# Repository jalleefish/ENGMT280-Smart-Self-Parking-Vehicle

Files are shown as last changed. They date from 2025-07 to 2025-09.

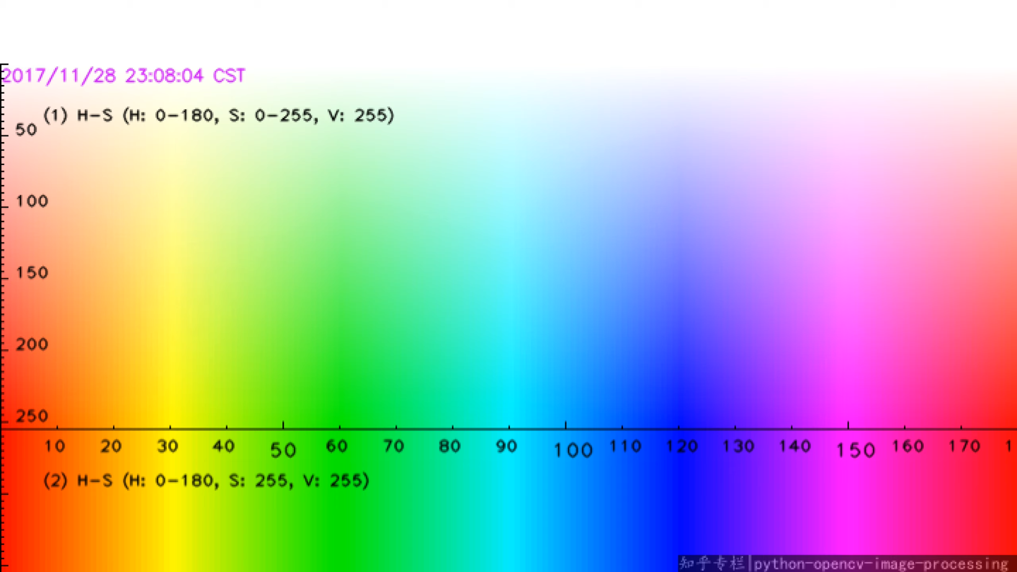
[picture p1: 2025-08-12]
System Logic/Drafts/Image Processing Code/HSV Colour Chart.png

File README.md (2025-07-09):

# ENGMT280-Smart-Self-Parking-Vehicle
ENGMT280/ENGEE281 – 25B
Smart Self-parking Vehicle – Design Rules
A scaled version of a typical car park layout will be setup in D.2.03 and C.1.12 (eventually). So
please make sure to feel free to switch lab spaces during the later half of the trimester to have a
go at testing your systems on the track. Below are the design requirements and design constraints
that needs to met by the Smart self-parking vehicle (SSV) you design, while meeting the event
regulations.




Fig. 1(top). Arena for the SSV showing the starting point and the parking bays and (bottom)
Colored tiles placed at the parking bay’s rear wall and parking sensors to check successful vehicle
parking.
ENGMT280/ENGEE281 – 25B
1. Your SAV, once ‘started’, should be able to complete the task autonomously – i.e., no user
inputs from any sort of wired or wireless communication sources once the SSV starts to move.
2. The only form of external communication once your SSV starts is the camera feed going
between the SSV and your laptop/pc for image processing and the processed image’s info
being sent back to the SSV.
3. The SSV, before it’s switched ‘on’, should be completely within the starting area of the arena
(highlighted by the engraved box along the bottom part of the arena in Fig 1(top))
4. There is no restriction for which side can be chosen to start the SSV from as the arena is
symmetric along the vertical axis as seen from Fig 1 (top)’s orientation. The SSV design team
can choose their preferred starting side. If starting from the left-hand side, the SSV needs to
reverse while steering left into parking position and if starting from the right-hand side, the
SSV needs to reverse while steering right back into the parking bay.
5. There will be a reference tile after the starting point where the reference-coloured tile will
be placed that indicates the color of the parking bay that the SSV can park at.
6. The SSV needs to be able to travel along the parking area’s length while checking for available
spots and simultaneously check if that available spot is indeed a valid parking spot.
7. The reference color tile that the SSV needs to scan will be bicolored or single colored
depending on the event.
8. A bi-colored tile indicates that the 2 different spots the SSV should park at in sequence. For
instance if the reference tile is half red and half yellow, the SSV should park in both spots one
after the other in any order.
9. As a minimum requirement, the SSV should atleast be able to park at a single spot (teams can
request a single-colored tile if that’s all they manage to scan and park at). However, marks
will be awarded accordingly.
10. The scoring sheet will be made available on Moodle near the second half of the trimester.
11. The SSV can in no way cause any damage to any part of the arena including the dummy car
models placed in the parked spots.
12. The overall dimensional and dynamic constraints for the SSV are given below
a. Max Length of SSV – 180 mm
b. Max width of SSV – 80 mm
c. Max height of SSV – 75 mm
d. Absolute wheelbase of the SSV – 120 mm
e. The minimum turning radius for the SSV is – 245.346096 mm (represents the half of
the diametrical distance between the outer wheels of the rear axle of the SSV, while
making an exact 180° turn).
f. The SSV shall not have a differential
drive arrangement (not to be confused
with the use of differential gearbox)
where one wheel is driven intentionally
at a rate different from the other wheel
on the same axle that causes the chassis
to pivot with a sharper turning radius
(see Fig 2 for an example of differential
drive robot) Fig.2. Example of a differential drive
robot (which is not allowed)



ENGMT280/ENGEE281 – 25B
g. If the use of some standard parts causes the width of the SSV to be slightly higher than
the allowed SSV width, the teaching team may allow it.
14. All the colored tiles and the reference tile will only be placed after the SSV starts moving.
15. The order of colours tiles placed in the slots will be at random, and their orders will be
changed between each team’s runs.
16. The reference-colored tile will be placed before the SSV reaches the location.



17. The SSVs needs to stop within the correctly identiϐied parking bay’s engraved area and should
not bump the rear walls/colored tiles.
Fig. 2. Rendering showing what the dummy car placements will be like
18. Dummy model cars will also be placed at random creating randomized open parking bays in
the arena.
19. The dummy model cars will not have the same color as the colored tiles that would be
randomly placed to avoid ambiguity.
20. If the randomly chosen reference-color tile has a color that already has the dummy model
cars creating a situation where no valid parking bays are present, the SSV should continue
forward and come to a safe stop within the engraved area opposite to the starting spot.
21. Apart from the batteries provided, no other energy sources can be added to the SSV.
Components like elastic bands and light springs will be considered on a case-by-case basis.
(Make sure to consult before design decisions are made if using such energy storage devices).
22. All SSVs will be inspected to ensure unauthorized items are not present on the system and
they completely comply with all the dimensional and dynamic constraints.
23. SAVs considered unsafe to the users/ spectators/university buildings etc., will be disqualiϐied
at the discretion of the teaching team. Take care to consider H&S risk elements such as sharp
edges, ϐinger traps, electrical shorts, etc., and address them appropriately.
24. A list of available materials will be made available on Moodle under ‘design project resources’
section. Any speciϐic equipment if needed, needs to have prior permission obtained.
25. Under the discretion of the teaching team, 3D printing of parts may be allowed if its within a
volume of 3000 mm3 and merits the shape complexity that cannot be otherwise
manufactured using conventional fabrication approach.
ENGMT280/ENGEE281 – 25B
26. As an optional part, the teams can obtain a vacuformed body shell similar to that of the
dummy model car to put over your design. As such, the teams design should ensure all
electronics are within this envelope. Cut outs can be made on the vacuformed body shell to
allow for uninterrupted operation of any sensors.
27. YOUR SSV SHOULD BE CAPABLE OF ADAPTING TO THE CHANGING LIGHTING CONDITIONS
THROUGHOUT THE DAY ACROSS THE TRIMESTER. Any complaints that the lighting is too
harsh or varying will not be tolerated.
28. You will be given 3 tries to ϐinish your run and the best time of the three runs will be taken
for ϐinal grading.
29. If you have any queries on a speciϐic rule, please reach out for clariϐication. Do not assume
your own interpretation of a rule to be correct and have that as the deciding factor for any
design decisions made if there is any ambiguity in a rule.
Rule updates since ϐirst upload

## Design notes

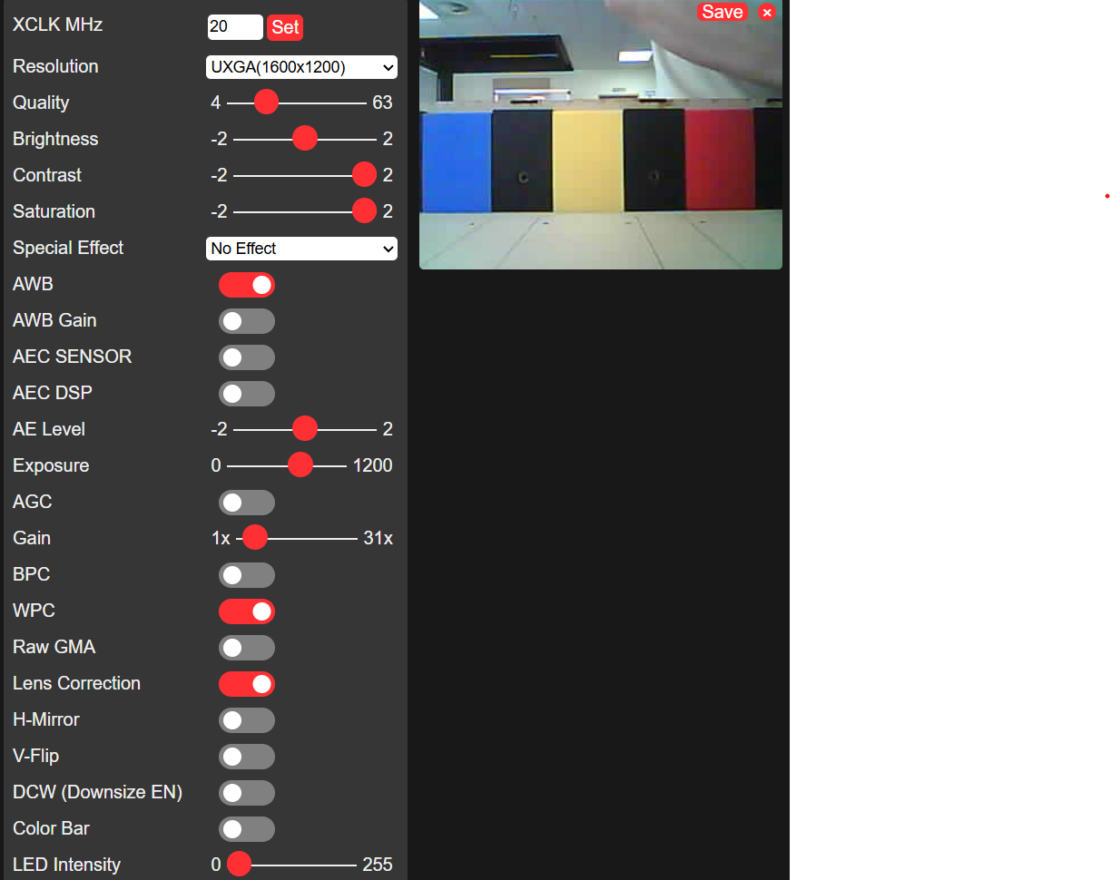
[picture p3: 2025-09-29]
ESP32 Camera Code/Camera Settings.png

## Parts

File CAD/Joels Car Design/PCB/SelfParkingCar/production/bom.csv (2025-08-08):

Designator | Footprint | Quantity | Value | LCSC Part #
BAT1 | 18650 Battery Holder | 1 | ~
CAM1, CAM3 | ESP32 Camera | 2 | ~
CAM2 | ESP32-CAM | 1 | ESP32-CAM
DRV1 | DRV8835 Motor Driver | 1 | ~
MOT1 | N20 Motor | 1 | ~
RNG1, RNG2, RNG3, RNG4, RNG5 | Range Sensor | 5 | ~
SER1 | S-G90 Servo | 1 | ~
U1 | ESP32-DevKitC | 1 | ESP32-DevKitC
VREG1, VREG2 | S13V30F5 Voltage Regulator | 2 | ~

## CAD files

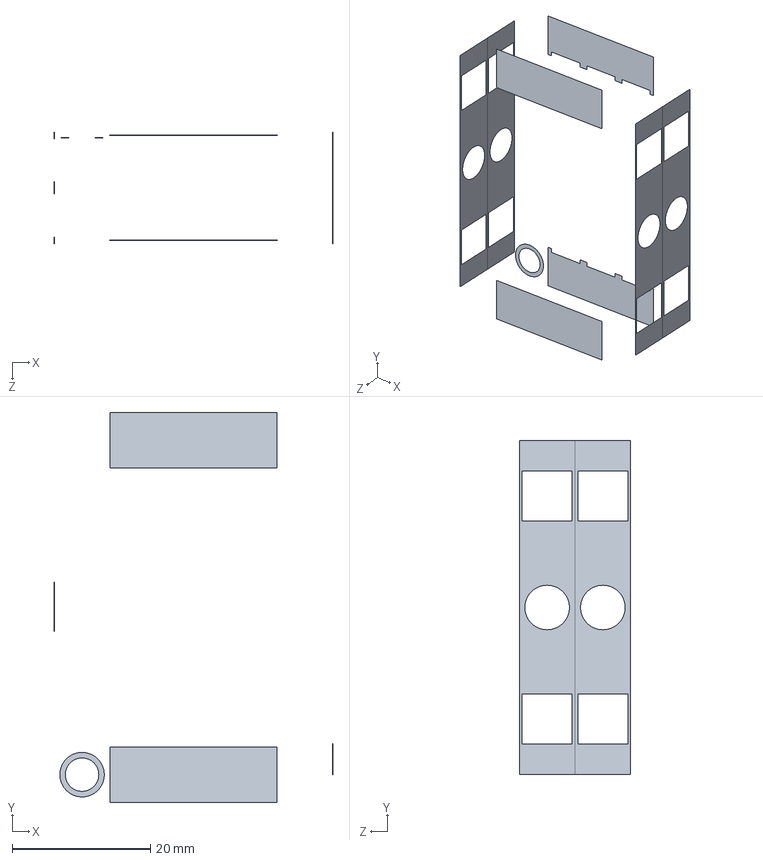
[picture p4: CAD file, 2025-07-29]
CAD/Joels Car Design/Diff Assembly Fixed1.SLDPRT
40.4 x 56.5 x 16.1 mm

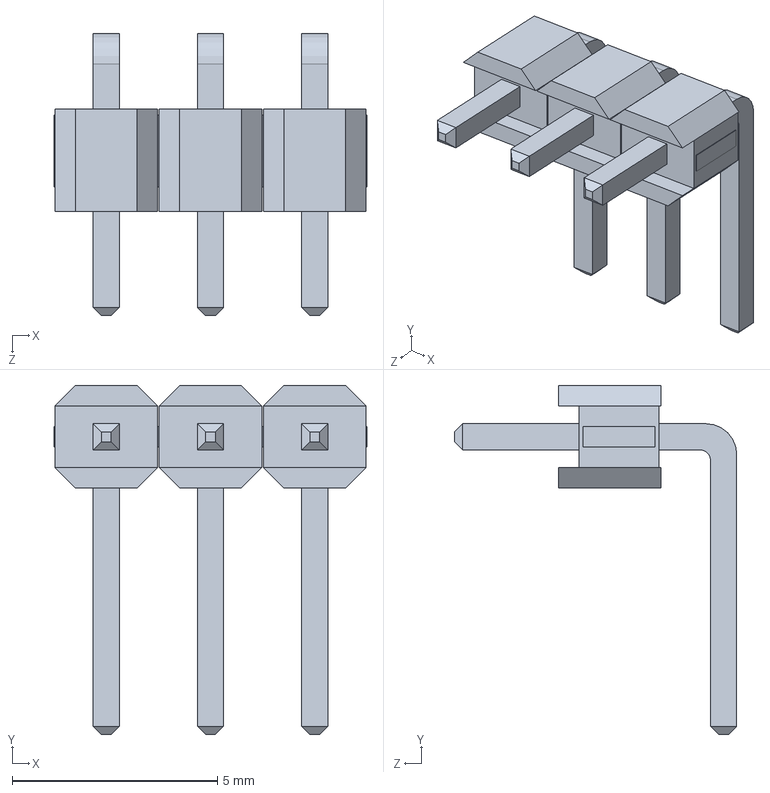
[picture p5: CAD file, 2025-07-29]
CAD/Joels Car Design/Range Sensor.SLDASM
7.62 x 8.50 x 6.88 mm
angled_headers x 3

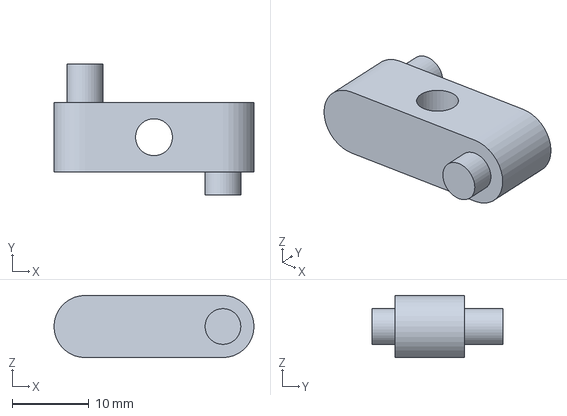
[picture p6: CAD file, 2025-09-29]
CAD/Joels Car Design/3D Printing/Steering Wheels Mount2.3MF
26.0 x 17.0 x 8.07 mm

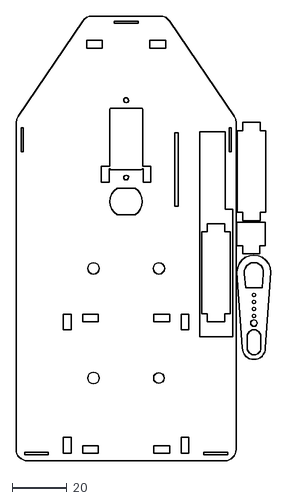
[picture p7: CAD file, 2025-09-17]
CAD/Joels Car Design/Laser Cutting/ACR_3MM.dxf
93.1 x 162.4

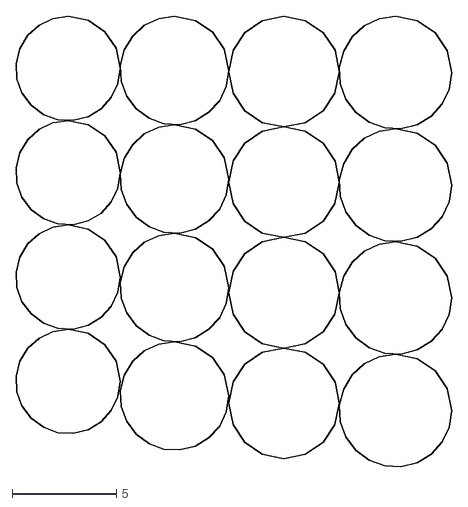
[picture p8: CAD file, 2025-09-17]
CAD/Joels Car Design/Laser Cutting/ACR_6MM.dxf
20.9 x 21.6

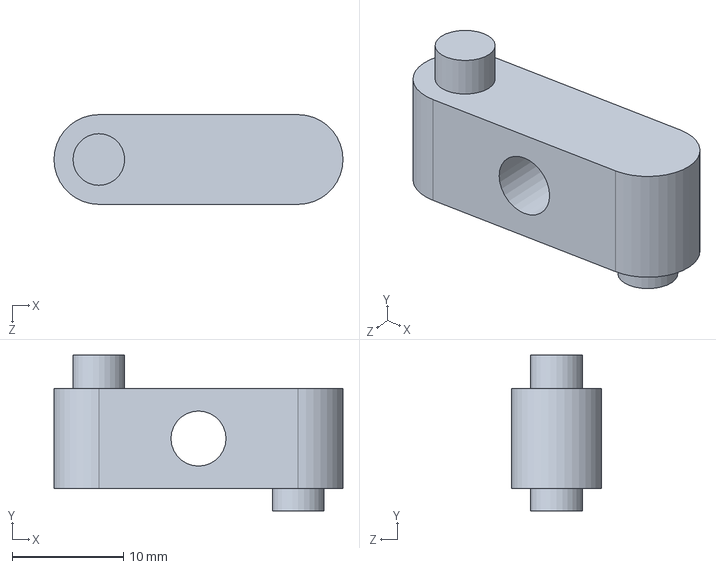
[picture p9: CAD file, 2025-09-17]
CAD/Joels Car Design/Steering Wheels Mount.SLDPRT
26.0 x 14.0 x 8.07 mm

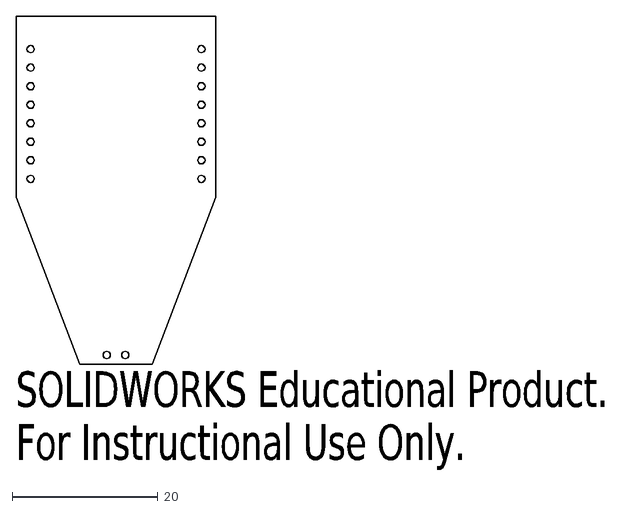
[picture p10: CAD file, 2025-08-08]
CAD/Joels Car Design/Camera.DXF
SOLIDWORKS Educational Product.
For Instructional Use Only.

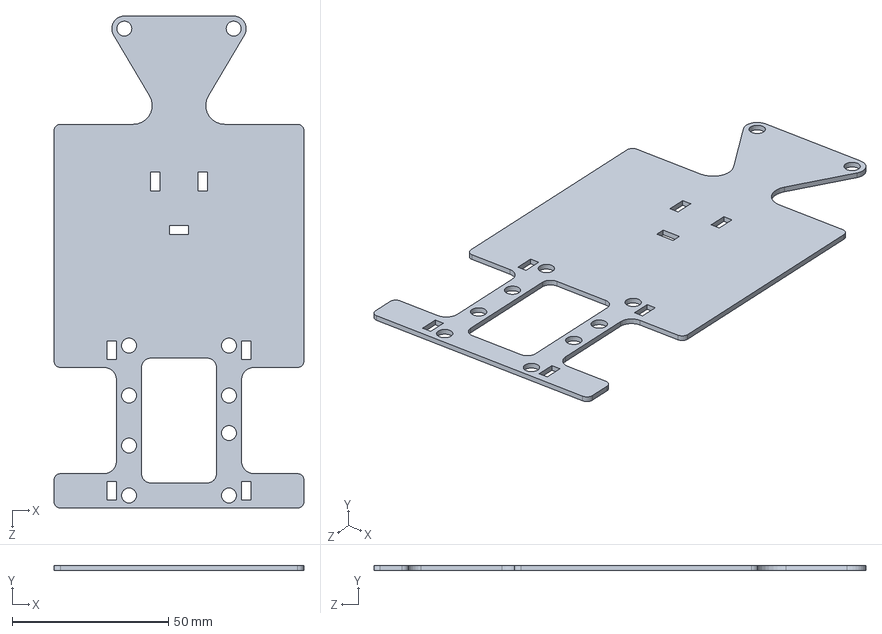
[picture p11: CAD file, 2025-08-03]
CAD/Joels Car Design/Base.SLDPRT
80.0 x 1.57 x 157.5 mm

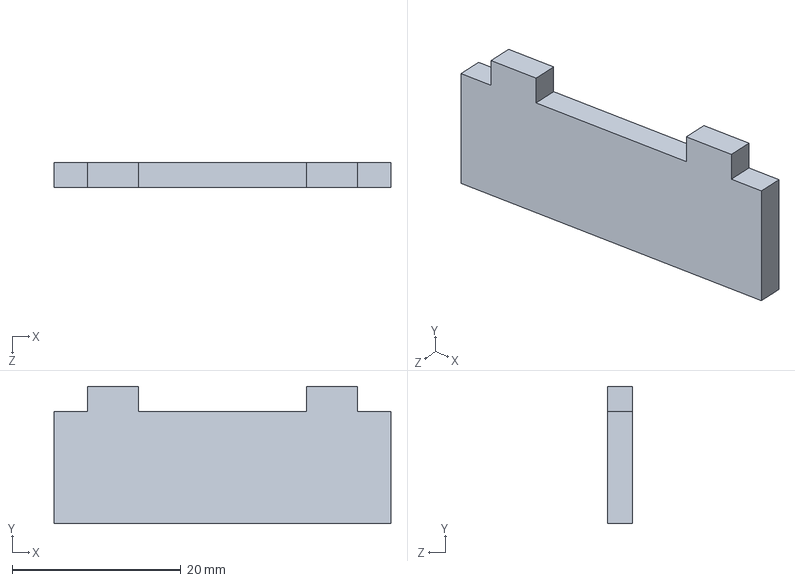
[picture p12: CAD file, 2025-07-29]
CAD/Joels Car Design/Diff Clamp.SLDPRT
40.0 x 16.3 x 3.00 mm

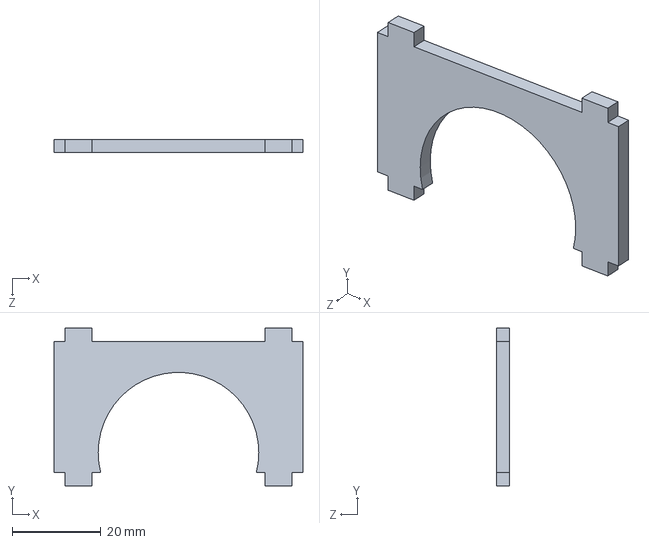
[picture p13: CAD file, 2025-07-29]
CAD/Joels Car Design/Rear Mid Support.SLDPRT
56.0 x 35.5 x 3.00 mm

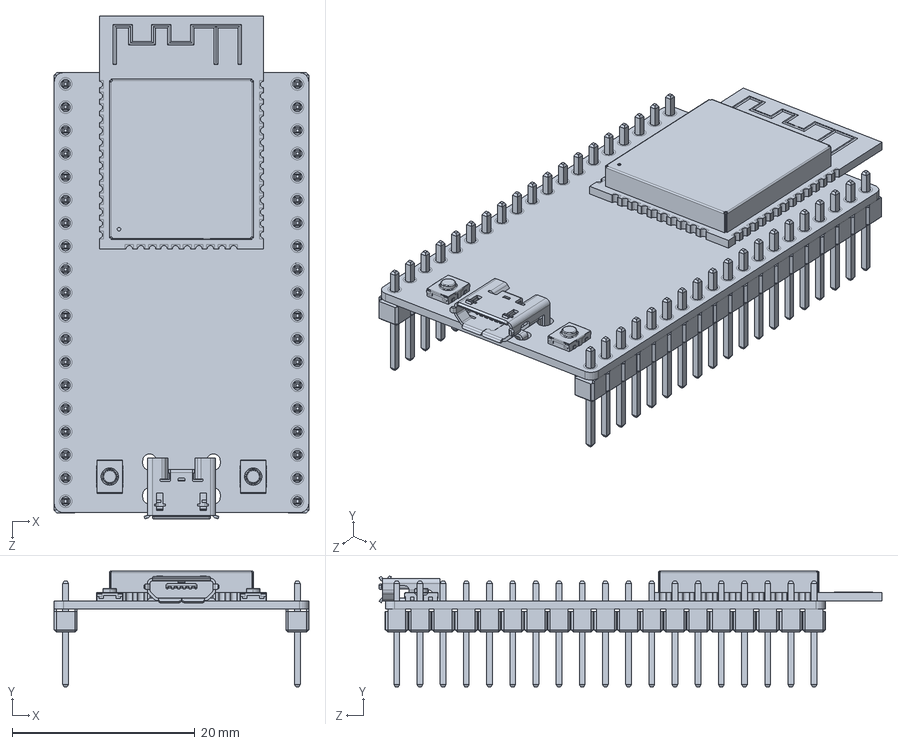
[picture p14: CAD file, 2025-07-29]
CAD/Joels Car Design/ESP32.SLDPRT
27.9 x 12.7 x 55.1 mm

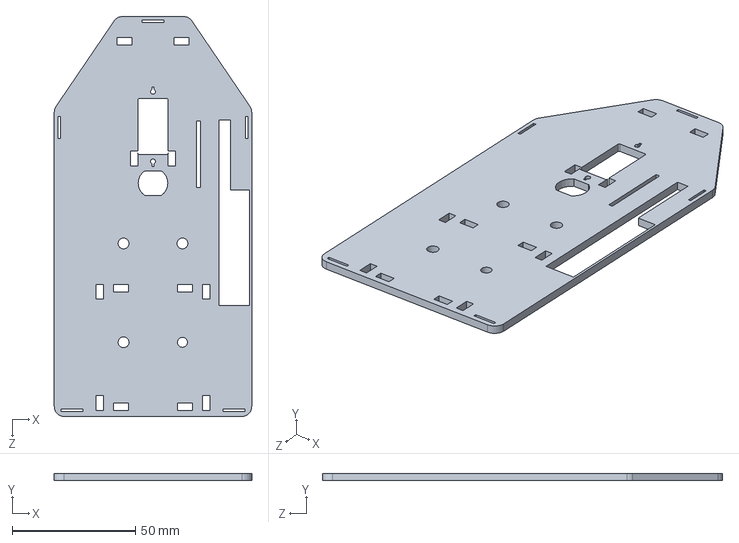
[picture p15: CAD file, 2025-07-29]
CAD/Joels Car Design/Mid Base.SLDPRT
80.0 x 3.00 x 162.0 mm

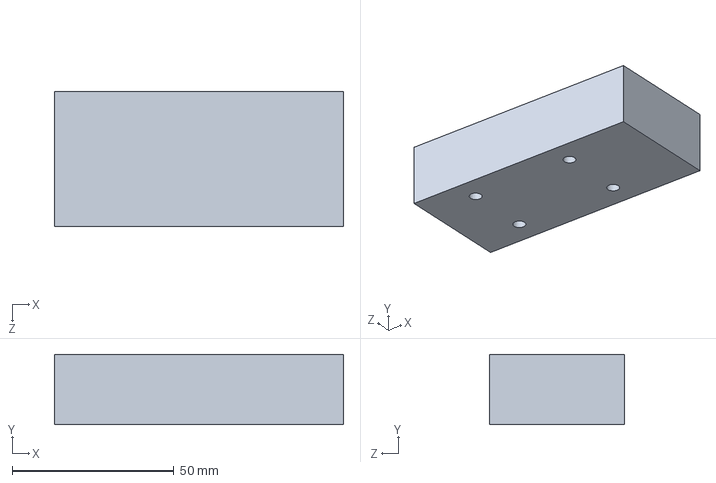
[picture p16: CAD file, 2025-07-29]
CAD/Joels Car Design/Battery Container.SLDPRT
89.4 x 21.8 x 41.8 mm

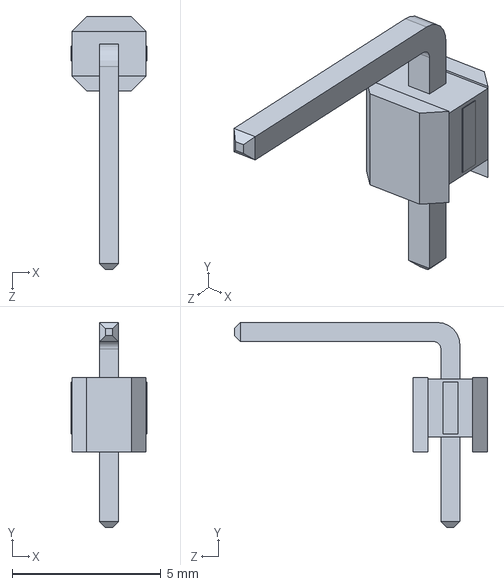
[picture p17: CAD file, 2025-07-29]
CAD/Joels Car Design/angled_headers.SLDPRT
2.54 x 6.88 x 8.50 mm

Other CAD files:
CAD/Joels Car Design/Car Design.SLDASM
CAD/Joels Car Design/Camera Assembly.SLDASM
CAD/Joels Car Design/Voltage Regulator.SLDASM
CAD/Joels Car Design/Motor Controller.SLDASM
CAD/Joels Car Design/20mmCoupler.SLDPRT
CAD/Joels Car Design/3D Printing/Steering Wheels Mount.3MF
CAD/Joels Car Design/3D Printing/Steering Wheels Mount.STL
CAD/Joels Car Design/All Laser Cut.SLDDRW
CAD/Joels Car Design/Camera Mount.SLDPRT
CAD/Joels Car Design/Car Design.DXF
CAD/Joels Car Design/ESP32 CAM.SLDPRT
CAD/Joels Car Design/Front Mid Support.SLDPRT
CAD/Joels Car Design/Front Wheel.SLDPRT
CAD/Joels Car Design/Long Steering Pin.SLDPRT
CAD/Joels Car Design/Motor Controller.SLDPRT
CAD/Joels Car Design/Motor Support.SLDPRT
CAD/Joels Car Design/Range Sensor.SLDPRT
CAD/Joels Car Design/Right Angle Motor N20.SLDPRT
CAD/Joels Car Design/Servo Horn.SLDPRT
CAD/Joels Car Design/Servo Motor.SLDPRT
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

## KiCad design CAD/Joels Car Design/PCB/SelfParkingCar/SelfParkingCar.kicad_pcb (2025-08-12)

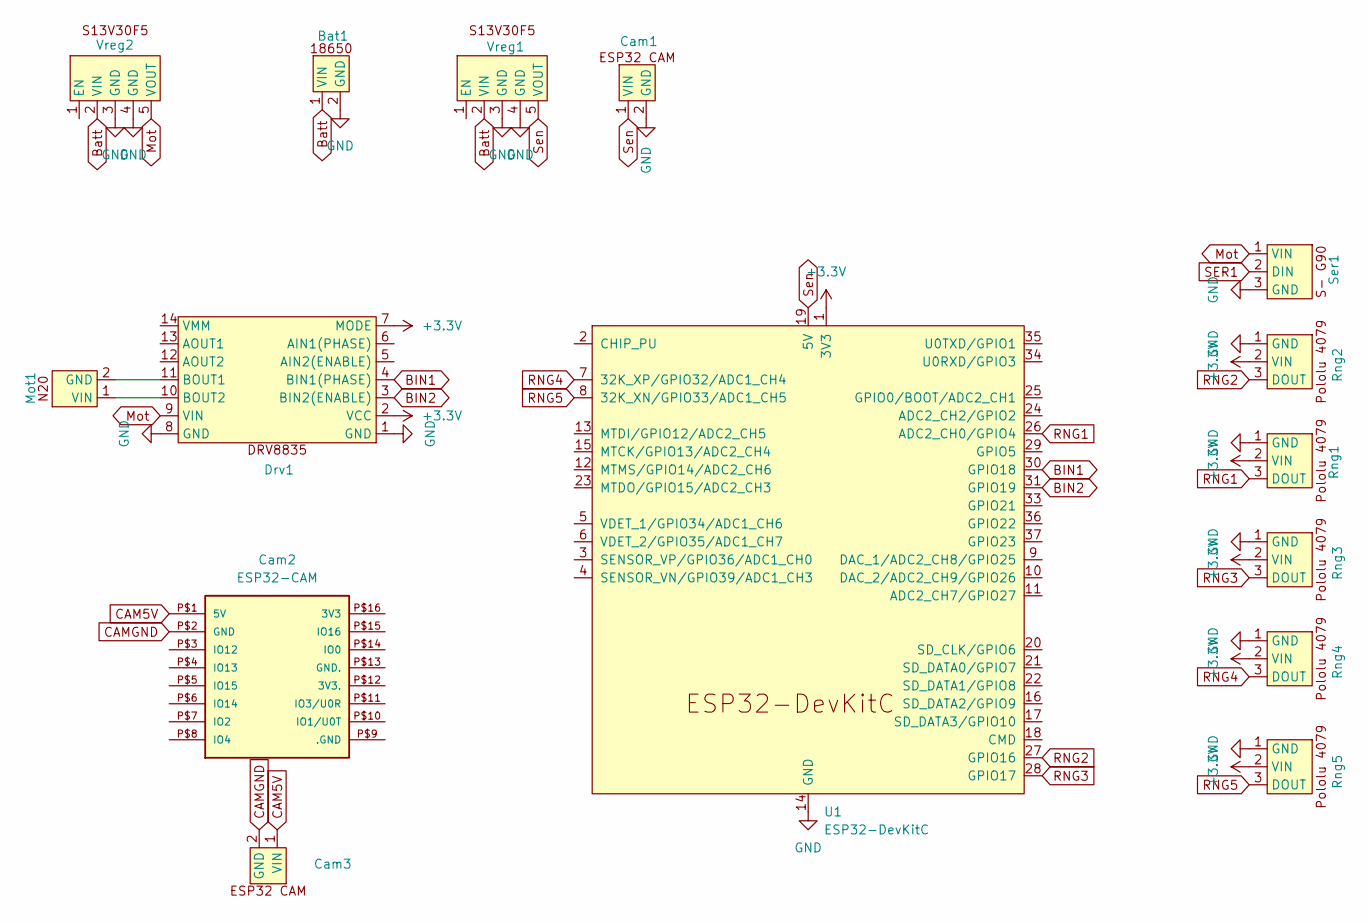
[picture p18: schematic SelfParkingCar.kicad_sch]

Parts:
Bat1: 18650 Battery Holder
Cam1, Cam3: ESP32 Camera
Cam2: ESP32-CAM
Drv1: DRV8835 Motor Driver
Mot1: N20 Motor
Rng1, Rng2, Rng3, Rng4, Rng5: Range Sensor
Ser1: S-G90 Servo
U1: ESP32-DevKitC
Vreg1, Vreg2: S13V30F5 Voltage Regulator

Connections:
+3.3V: Drv1.2 (VCC), Drv1.7 (MODE), Rng1.2 (VIN), Rng2.2 (VIN), Rng3.2 (VIN), Rng4.2 (VIN), Rng5.2 (VIN), U1.1 (3V3)
BIN1: Drv1.4 (BIN1(PHASE)), U1.30 (GPIO18)
BIN2: Drv1.3 (BIN2(ENABLE)), U1.31 (GPIO19)
Batt: Bat1.1 (VIN), Vreg1.2 (VIN), Vreg2.2 (VIN)
CAM5V: Cam2.P$1 (5V), Cam3.1 (VIN)
CAMGND: Cam2.P$2 (GND), Cam3.2 (GND)
GND: Bat1.2 (GND), Cam1.2 (GND), Drv1.1 (GND), Drv1.8 (GND), Rng1.1 (GND), Rng2.1 (GND), Rng3.1 (GND), Rng4.1 (GND), Rng5.1 (GND), Ser1.3 (GND), U1.14 (GND), U1.32 (GND), U1.38 (GND), Vreg1.3 (GND), Vreg1.4 (GND), Vreg2.3 (GND), Vreg2.4 (GND)
Mot: Drv1.9 (VIN), Ser1.1 (VIN), Vreg2.5 (VOUT)
unnamed: Drv1.11 (BOUT1), Mot1.2 (GND)
unnamed: Drv1.10 (BOUT2), Mot1.1 (VIN)
RNG1: Rng1.3 (DOUT), U1.26 (ADC2_CH0/GPIO4)
RNG2: Rng2.3 (DOUT), U1.27 (GPIO16)
RNG3: Rng3.3 (DOUT), U1.28 (GPIO17)
RNG4: Rng4.3 (DOUT), U1.7 (32K_XP/GPIO32/ADC1_CH4)
RNG5: Rng5.3 (DOUT), U1.8 (32K_XN/GPIO33/ADC1_CH5)
SER1: Ser1.2 (DIN)
Sen: Cam1.1 (VIN), U1.19 (5V), Vreg1.5 (VOUT)

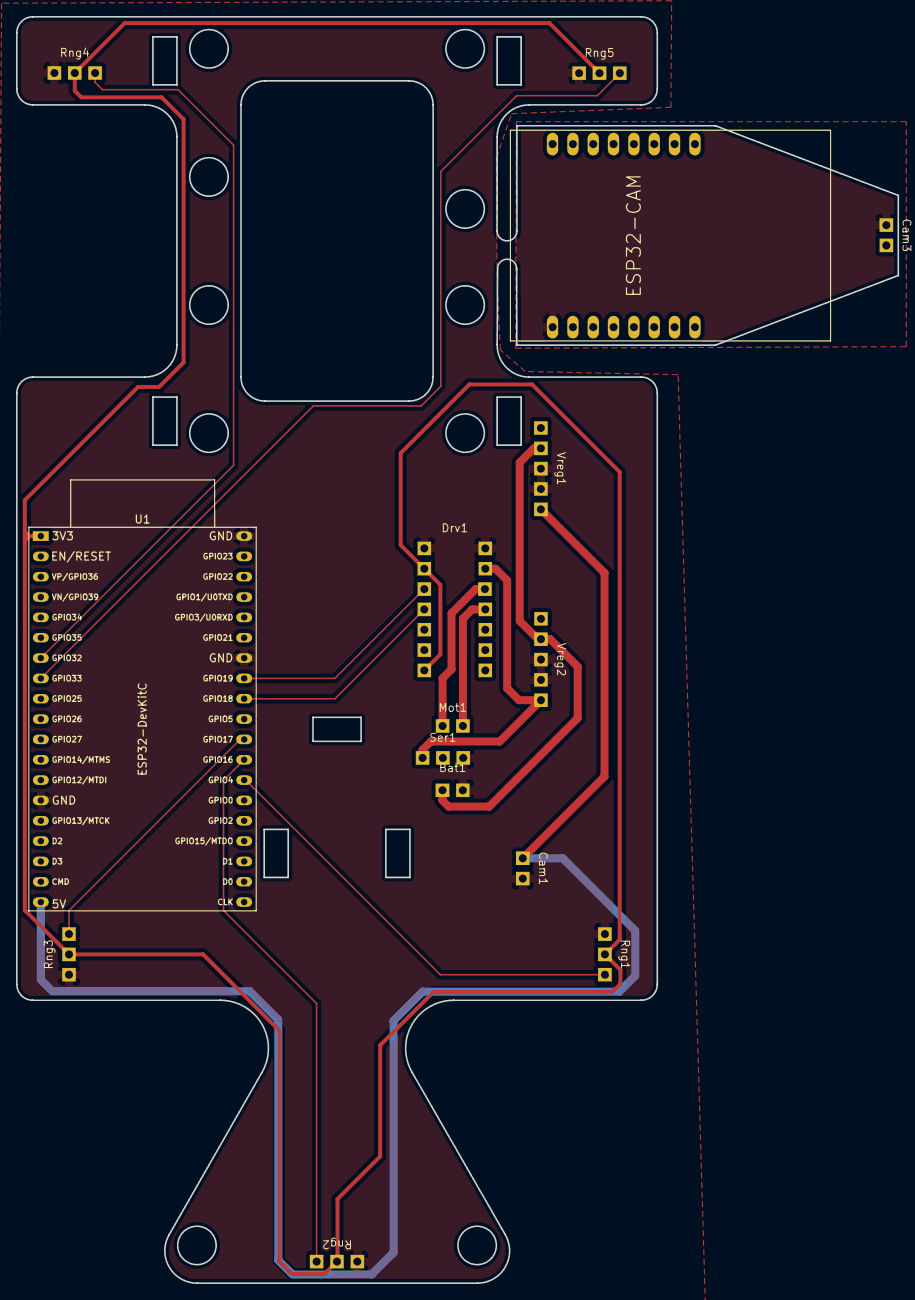
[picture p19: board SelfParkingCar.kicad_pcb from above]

Board: 2 copper layers, 110.1 x 158.2 mm, 15 parts (0 on the bottom side), 16 nets.

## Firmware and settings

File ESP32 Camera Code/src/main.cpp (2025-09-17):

#include "esp_camera.h"
#include <WiFi.h>

// ===========================
// Select camera model in board_config.h
// ===========================
#include "board_config.h"

// ===========================
// Enter your WiFi credentials
// ===========================
const char *ssid = "JOELS-LAPTOP";
const char *password = "28075851";

void startCameraServer();
void setupLedFlash();

void setup() {
  Serial.begin(115200);
  Serial.setDebugOutput(true);
  Serial.println();

  camera_config_t config;
  config.ledc_channel = LEDC_CHANNEL_0;
  config.ledc_timer = LEDC_TIMER_0;
  config.pin_d0 = Y2_GPIO_NUM;
  config.pin_d1 = Y3_GPIO_NUM;
  config.pin_d2 = Y4_GPIO_NUM;
  config.pin_d3 = Y5_GPIO_NUM;
  config.pin_d4 = Y6_GPIO_NUM;
  config.pin_d5 = Y7_GPIO_NUM;
  config.pin_d6 = Y8_GPIO_NUM;
  config.pin_d7 = Y9_GPIO_NUM;
  config.pin_xclk = XCLK_GPIO_NUM;
  config.pin_pclk = PCLK_GPIO_NUM;
  config.pin_vsync = VSYNC_GPIO_NUM;
  config.pin_href = HREF_GPIO_NUM;
  config.pin_sccb_sda = SIOD_GPIO_NUM;
  config.pin_sccb_scl = SIOC_GPIO_NUM;
  config.pin_pwdn = PWDN_GPIO_NUM;
  config.pin_reset = RESET_GPIO_NUM;
  config.xclk_freq_hz = 20000000;
  config.frame_size = FRAMESIZE_UXGA;
  config.pixel_format = PIXFORMAT_JPEG;  // for streaming
  //config.pixel_format = PIXFORMAT_RGB565; // for face detection/recognition
  config.grab_mode = CAMERA_GRAB_WHEN_EMPTY;
  config.fb_location = CAMERA_FB_IN_PSRAM;
  config.jpeg_quality = 12;
  config.fb_count = 1;

  // if PSRAM IC present, init with UXGA resolution and higher JPEG quality
  //                      for larger pre-allocated frame buffer.
  if (config.pixel_format == PIXFORMAT_JPEG) {
    if (psramFound()) {
      config.jpeg_quality = 10;
      config.fb_count = 2;
      config.grab_mode = CAMERA_GRAB_LATEST;
    } else {
      // Limit the frame size when PSRAM is not available
      config.frame_size = FRAMESIZE_SVGA;
      config.fb_location = CAMERA_FB_IN_DRAM;
    }
  } else {
    // Best option for face detection/recognition
    config.frame_size = FRAMESIZE_240X240;
#if CONFIG_IDF_TARGET_ESP32S3
    config.fb_count = 2;
#endif
  }

#if defined(CAMERA_MODEL_ESP_EYE)
  pinMode(13, INPUT_PULLUP);
  pinMode(14, INPUT_PULLUP);
#endif

  // camera init
  esp_err_t err = esp_camera_init(&config);
  if (err != ESP_OK) {
    Serial.printf("Camera init failed with error 0x%x", err);
    return;
  }

  sensor_t *s = esp_camera_sensor_get();
  // initial sensors are flipped vertically and colors are a bit saturated
  if (s->id.PID == OV3660_PID) {
    s->set_vflip(s, 1);        // flip it back
    s->set_brightness(s, 1);   // up the brightness just a bit
    s->set_saturation(s, -2);  // lower the saturation
  }
  // drop down frame size for higher initial frame rate
  if (config.pixel_format == PIXFORMAT_JPEG) {
    s->set_framesize(s, FRAMESIZE_QVGA);
  }

#if defined(CAMERA_MODEL_M5STACK_WIDE) || defined(CAMERA_MODEL_M5STACK_ESP32CAM)
  s->set_vflip(s, 1);
  s->set_hmirror(s, 1);
#endif

#if defined(CAMERA_MODEL_ESP32S3_EYE)
  s->set_vflip(s, 1);
#endif

// Setup LED FLash if LED pin is defined in camera_pins.h
#if defined(LED_GPIO_NUM)
  setupLedFlash();
#endif

  WiFi.begin(ssid, password);
  WiFi.setSleep(false);

  Serial.print("WiFi connecting");
  while (WiFi.status() != WL_CONNECTED) {
    delay(500);
    Serial.print(".");
  }
  Serial.println("");
  Serial.println("WiFi connected");

  startCameraServer();

  Serial.print("Camera Ready! Use 'http://");
  Serial.print(WiFi.localIP());
  Serial.println("' to connect");
}

void loop() {
  // Do nothing. Everything is done in another task by the web server
  delay(10000);
}

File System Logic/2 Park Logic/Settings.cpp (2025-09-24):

// Settings.cpp
// This file contains the settings and configurations for the Self Parking Car project.
#include "Settings.h"
#include "DistanceSensors.h"
#include "MotorControl.h"
#include "ServoMotorControl.h"
#include "Communications.h"
#include "SystemLogic.h"

// Distance Sensor Pins
const uint8_t  DistPin1 = 4;  // sensor 1 OUT pin
const uint8_t  DistPin2 = 16;  // sensor 2 OUT pin
const uint8_t  DistPin3 = 17;  // sensor 3 OUT pin
const uint8_t  DistPin4 = 32;  // sensor 4 OUT pin
const uint8_t  DistPin5 = 33;  // sensor 5 OUT pin

// Motor Pins
const int  MotorDirection = 18;  // High=forward, Low=reverse
const int  MotorSpeed = 19;  // High=on, Low=off

// Servo Motor Pins
const int  ServoPin = 21;  // servo motor 1 control pin

// Replace with your network credentials
const char* ssid = "JOELS-LAPTOP";  // Enter SSID here
const char* password = "28075851";  //Enter Password here
const char* host = "192.168.137.1";  // your laptop's IP
const int port = 5000;

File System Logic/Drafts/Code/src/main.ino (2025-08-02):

// main.ino
// This file is the main entry point for the Self Parking Car project.
#include <Arduino.h>
#include "Settings.h"
#include "DistanceSensors.h"
#include "MotorControl.h"
#include "ServoMotorControl.h"

void setup() {
    Serial.begin(115200);
    setupDist();
    setupMotor();
    setupServo();
}

void loop() {
    updateDist();
    motorForward();  // test run
    delay(1000);
    motorStop();
    delay(100);  // Adjust delay as needed
    servoLeft();  // test servo motor
    servoRight();  // test servo motor
    delay(1000);
    servoMiddle();  // reset servo motor to middle position
}

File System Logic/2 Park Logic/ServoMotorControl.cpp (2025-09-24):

// ServoMotorControl.cpp
// This file contains the implementation of servo motor functionalities for the Self Parking Car project.
#include <Arduino.h>
#include "Settings.h"
#include "DistanceSensors.h"
#include "MotorControl.h"
#include "ServoMotorControl.h"
#include "Communications.h"
#include "SystemLogic.h"
#include <ESP32Servo.h>

Servo myServo;

void setupServo() {
	// Allow allocation of all timers
	ESP32PWM::allocateTimer(0);
	ESP32PWM::allocateTimer(1);
	ESP32PWM::allocateTimer(2);
	ESP32PWM::allocateTimer(3);
	myServo.setPeriodHertz(50);    // standard 50 hz servo
	myServo.attach(ServoPin, 500, 2400); // attaches the servo on pin 18 to the servo object
	// using default min/max of 1000us and 2000us
	// different servos may require different min/max settings
	// for an accurate 0 to 180 sweep
    myServo.write(98);  // Move to 0 degrees
    Serial.println("Servo motor initialized");
    delay(15);        // wait for a second
}

void steering(int degree) {
    if (degree < 73) degree = 73;
    if (degree > 123) degree = 123;
    myServo.write(degree);
}

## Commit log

2025-07-09 ESP32 Code Setup
2025-07-09 CAD Models
    [FS09R_Servo_Motor.SLDPRT, angled_headers.SLDPRT, angled_receptacles.SLDPRT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]
2025-07-10 All 3D Models
    [ESP32 CAM MB.SLDPRT, FS09R_Servo_Motor.SLDPRT, Joel Design 1.SLDASM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]
2025-07-17 Design Update
    [Base.SLDPRT, Battery Container.SLDPRT, Diff Assembly Fixed.SLDPRT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]
2025-07-29 CAD complete, laser cutting setup
    [10mmCoupler.SLDPRT, 15mmCoupler.SLDPRT, 20mmCoupler.SLDPRT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]
2025-07-31 Distance Sensor Code Test
    [ACR_3MM Nested.dxf, ACR_6MM Nested.dxf]
2025-08-01 5 Distance Sensors & Motor Control
2025-08-02 Clean Up
    [10mmCoupler.SLDPRT, 15mmCoupler.SLDPRT, 20mmCoupler.SLDPRT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]
2025-08-03 PCB Design Prototype
    [Base.SLDPRT, Car Design.DXF, Car Design.SLDASM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]
2025-08-08 PCB Complete
    [Camera.DXF, SelfParkingCar.kicad_pcb, SelfParkingCar.kicad_sch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]
2025-08-12 Code for camera working (unreliable)
    [SelfParkingCar.kicad_pcb]
2025-08-12 PCB Joel's Final Design
    [SelfParkingCar.kicad_pcb, positions.csv]
2025-09-17 A whole lotta stuff
    [ACR_3MM Nested.dxf, ACR_3MM.dxf, ACR_6MM Nested.dxf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]
2025-09-25 HE DO THE WIBBLE WOBBLE
    [MotorControl.cpp, SystemLogic.cpp]
2025-09-30 Camera Working, Needs white bal
2025-09-30 Working park detection, white ballence calibration fix in progress. Needs park logic
    [Communications.cpp]
2025-10-03 Distance Sensors fixed
2025-10-14 Final Code using 2 Parks
    [Car Design.SLDASM]
